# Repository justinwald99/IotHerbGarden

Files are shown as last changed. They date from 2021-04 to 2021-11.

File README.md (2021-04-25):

# iot_herb_garden

## Installation / Environment Settings
In order prepare your environment to run the IoT Herb Garden System, first install python and the following python packages using the command "pip install {package name}" on both the computer and Rasperry Pi used for your system. The versions listed in the table are those that we ran the project with, but many packages will work with later versions.

| Package | Version |
|---| ---|
| Brotli | 1.0.9 |
| click | 7.1.2 |
| colorama | 0.4.4 |
| dash | 1.19.0 |
| dash-bootstrap-components | 0.12.0 |
| dash-core-components | 1.15.0 |
| dash-html-components | 1.1.2 |
| dash-renderer | 1.9.0 |
| dash-table | 4.11.2 |
| Flask | 1.1.2 |
| Flask-Compress | 1.9.0 |
| future | 0.18.2 |
| greenlet | 1.0.0 |
| itsdangerous | 1.1.0 |
| Jinja2 | 2.11.3 |
| MarkupSafe | 1.1.1 |
| numpy | 1.20.2 |
| paho-mqtt | 1.5.1 |
| pandas | 1.2.3 |
| pip | 20.2.3 |
| plotly | 4.14.3 |
| python-dateutil | 2.8.1 |
| pytz | 2021.1 |
| retrying | 1.3.3 |
| setuptools | 49.2.1 |
| six | 1.15.0 |
| SQLAlchemy | 1.4.9 |
| Werkzeug | 1.0.1 |

You will also need a working MQTT broker, and a wireless network to run the local system on. We used `mosquitto`, accessible from https://mosquitto.org/ . Mosquitto configuration file needs to contain the settings:
```
listener 1883
allow_anonymous true
```

Next, assemble the hardware following the schematic in `docs/iot_herb_garden_schematic_bb.png` using the parts list in `docs/report.pdf` or other compatable parts.

## Running IoT_Herb_Garden / How to Run the Code

Three programs must be run to operate the IoT_Herb_Garden system: `garden_manager.py`, `garden_monitor.py`, and `garden_web_server.py`, as well as the MQTT broker.

When running the system, `garden_monitor.py` must be run on the Raspberry Pi. We recommended that `garden_manager.py` and `garden_web_server.py` be run on a separate computer to increase performance, but they can be run from the Pi if you chose (note that both manager and web server must be run on the same machine due to requiring direct database access).

To start the system, first start the MQTT server. If using mosquittor, run the following command from the mosquitto directory:
```
mosquitto -c "{address of the config file}"
```

Next start `garden_manager.py` using the command:
```
python garden_manager.py {ip of MQTT broker}
```

Next start `garden_web_server.py` using the command:
```
python garden_web_server.py {ip of MQTT broker}
```

Next start `garden_monitor.py` using the command:
```
python garden_monitor.py {ip of MQTT broker}
```

At this point all portions of the system should be online. The web server can be accessed through most browsers using `localhost:{port}` where port can be found in the command line output of `garden_web_server.py`. Each program can be stopped individually without impacting the rest of the system, other than the MQTT broker, which when closed would require a full system restart.

## Operations / How to Interpret the Results

To view the status of the system and manage sensor and plant settings, use the web server as described in the previous section. Through Overview and History, you can view the past sensor data and pump operations of the system. Controls can be used to manually operate the water pumps. Configurations can be used to change system settings on plant and sensor names, sensor sample rates, plant watering durations and soil humidity targets, and assign sensors and pumps to plants.

## Sample Input Files

Provided in the source code is a databse with data from our setup and testing. This data can be used through the web server to view how your data would look and test setting database values. Without any historical data, the system will generate a blank databse with default entries for plants and sensors. 

## Extra Information

This system was designed for a specific setup of four plants, but with minor alterations, many portions of the system could be extrapolated for larger or smaller setups. In order to understand the control flow and operations, we recommend reading the report found in `docs/`.

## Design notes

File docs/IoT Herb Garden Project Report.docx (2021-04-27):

CSC453: Internet of Things

April 25th, 2021

Parker Killian

Justin Wald

Michael Barger

Individual Contributions

Component | Weight | Parker Killian | Justin Wald | Michael Barger
Architecture Design | 0.1 | 33.3% | 33.3% | 33.3%
Frontend Design | 0.05 | 10% | 80% | 10%
Wiring Design | 0.05 | 20% | 40% | 40%
Hardware Assembly | 0.05 | 33.3% | 33.3% | 33.3%
Web Server | 0.15 | 50% | 30% | 20%
Garden Monitor | 0.15 | 50% | 25% | 25%
Garden Manager | 0.15 | 25% | 65% | 10%
Debugging | 0.1 | 10% | 10% | 80%
Presentation | 0.05 | 80% | 10% | 10%
Report | 0.1 | 20% | 40% | 40%
Documentation | 0.05 | 10% | 10% | 80%
Total Contributions | | 32.745% | 34.995% | 32.245%

# Introduction

When attempting to grow an herb garden, it can be difficult to remember to water your plants or to keep the soil humidity levels at an appropriate level. The objective of this project is to simplify this process by Internet of Things automation

The goal of this project was to create an automated garden management system that uses an array of sensors and water pumps to monitor the environment and automatically water the plants in an herb garden. This system would provide detailed information to the user of the status of their plants as well as allowing for a large amount of user customization to tailor the system to the user’s plants’ needs

# Design

## Architecture

IoT Herb Garden is comprised of 3 primary python scripts:

Garden Manager | Garden Monitor | Garden Web Server
- Create database schema objects. - Log sensor and event data to the database when received from the MQTT broker. - Provide auto-watering functionality. - Inform other components of configuration info read from the database. | - Configure defaults for sensors. - Collect and publish sensor data. - Activate water pumps when instructed to do so. | - Provide a web UI to interact with the Herb Garden - Display current metrics for sensors - Display a historic view of sensor values - Allow configuration of plant and sensor objects - Manually control pumps

Table 1: Script Overview

The separation of these three scripts gives the user flexibility in the hardware running each. The monitor script was kept lightweight to facilitate operation on an edge device such as a Raspberry Pi. Manager communicates with the monitor entirely through MQTT which means that it can run on an entirely different host, as long as they share the same broker. Web server does need access to the database to operate which ties it to running on the same host as manager since we used SQLite as our backend but with a little modification, web server could also run on its own host. Containerizing the entire system would be quite trivial thanks to this separation.

One other advantage of this architecture is that the more critical scripts, manager and monitor, could operate in “headless” mode without the web server running, only logging data to the DB. This also means that if the web server crashes for whatever reason, logging will continue.

Figure 1: MQTT architecture between the scripts

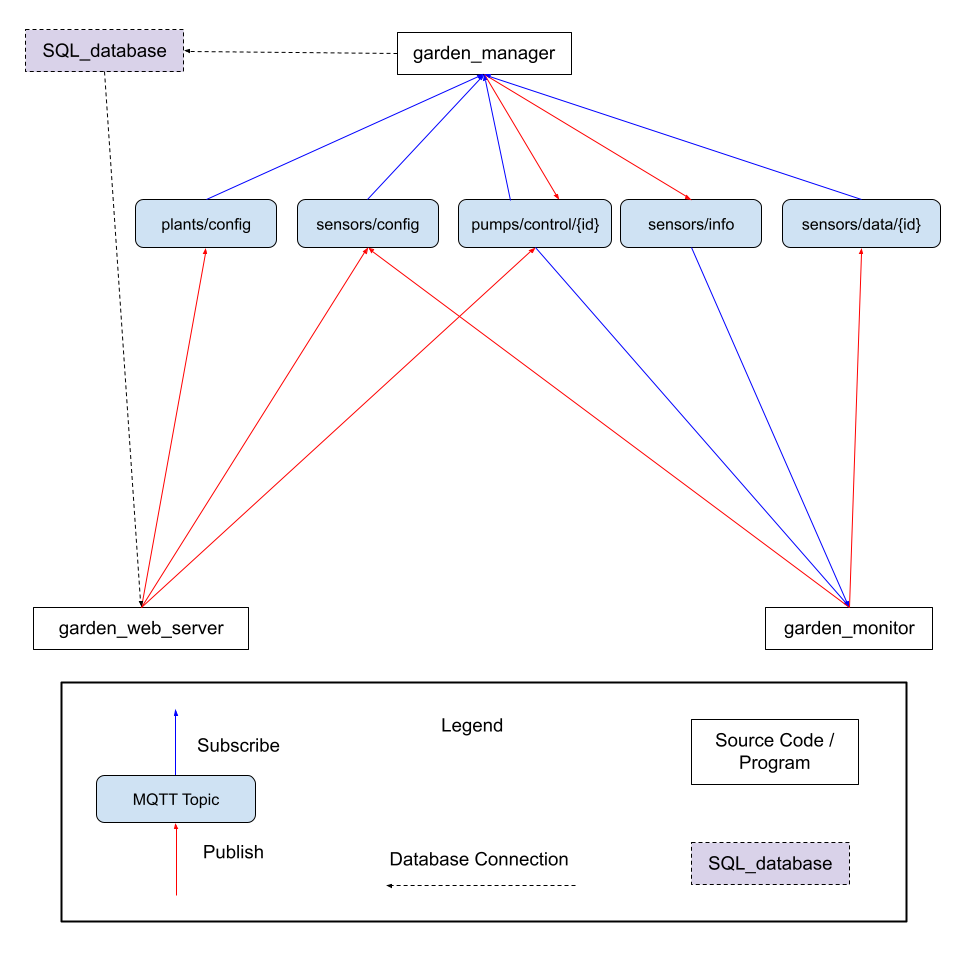
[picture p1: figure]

## MQTT

Communication between the different parts of our program is done primarily through MQTT, leveraging an outside broker. Below is a diagram showing the interaction between each component through MQTT messages. Each message contains a JSON payload (described in Appendix 1) to communicate the body of the messages.

A typical flow for the program is shown in figure 2 and follows these steps:

1. Monitor starts and begins logging sensor data with a default configuration file loaded from a static JSON File.
2. Manager reads any configuration data from the database and publishes this data to the sensors/info topic.
3. Monitor, which is subscribed to this topic, receives the information and compares it against the default values it has.
  a. If there are any differences, the information from the manager is preferred.
  b. If there are no sensors in the message published by the manager, such as in the case of a reset database, monitor publishes its default values to sensors/config, one at a time. Manager reads these messages and adds them to the sensors/info message.
4. Monitor begins sending sample messages to sensors/data.
5. Manager, subscribed to sensors/data, writes these messages to the database.
6. Manager also monitors sensor values to determine if watering is needed.

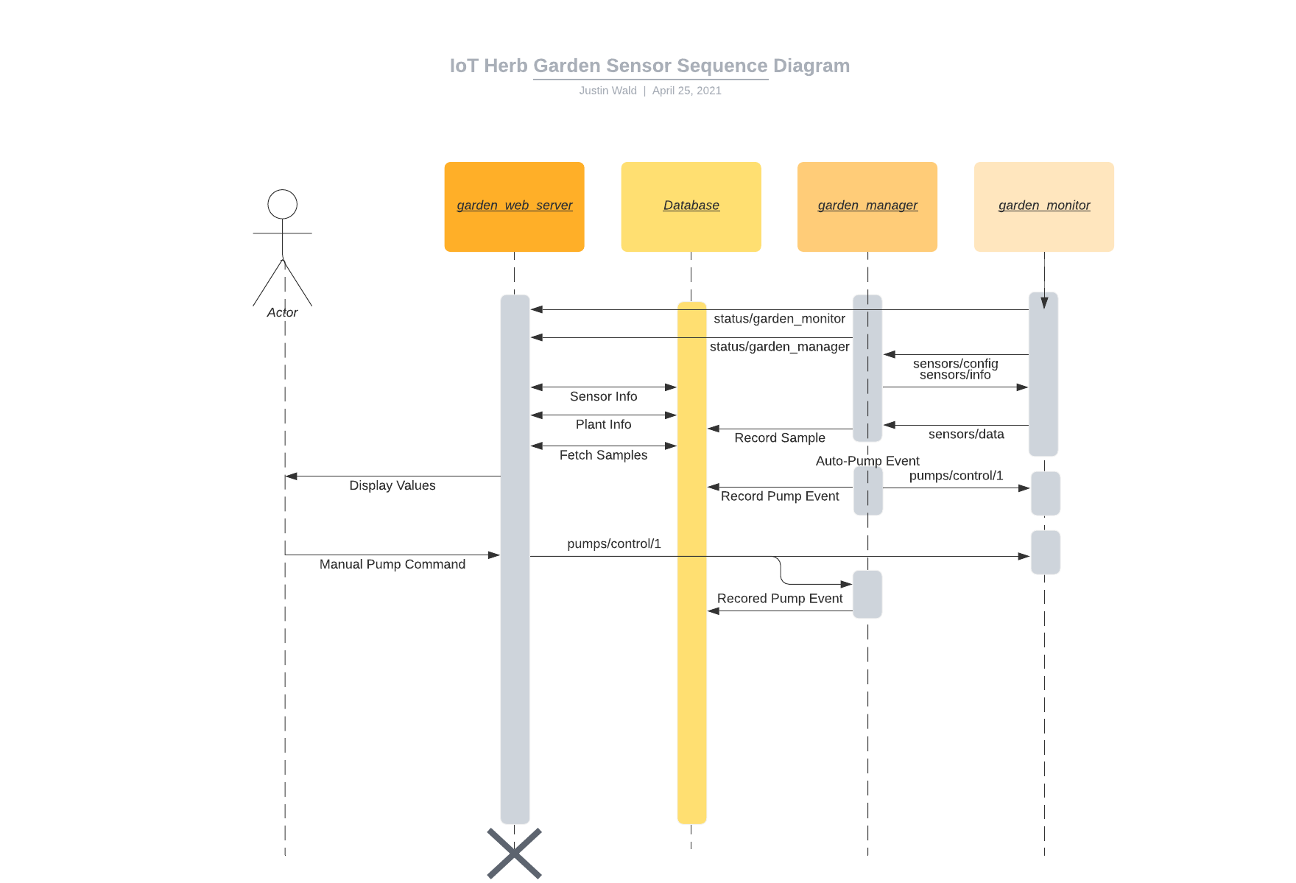
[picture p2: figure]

Figure 2: Sequence diagram of a basic flow through the system.

## Database

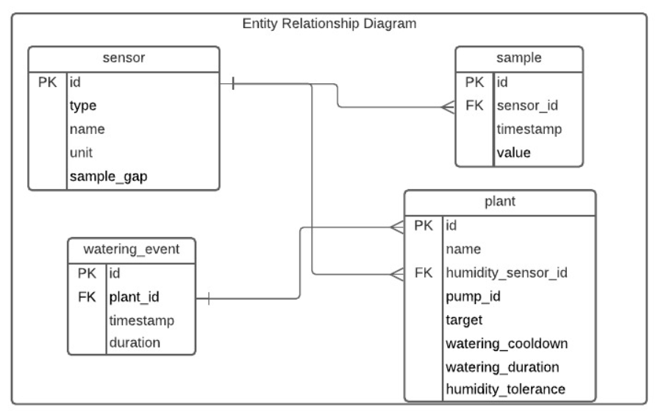
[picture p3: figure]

Figure 3: ERD diagram for the database.

The database is based on a SQLite backend which we accessed via SQLAlchemy for consistency and reliability. The database was used primarily to record data so that historical viewing was possible but it also enabled persistent settings to be specified by the user about the elements of the system.

## Web Server

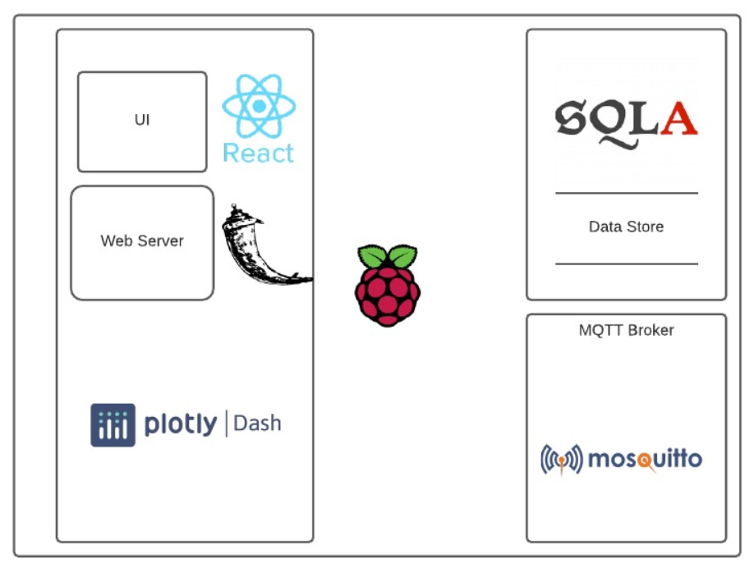
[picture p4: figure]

Figure 4: Technology overview.

The web server uses the Dash library which makes use of the highly popular Flask library for its web server operations while providing a robust React-based UI toolkit that includes the Plotly graphing library.

# Implementation

Our project runs on Python, using many public libraries for specific operations including SQLAlchemy, Dash, Dash Bootstrap Components, Pandas, Paho MQTT, and GPIOZero.

The hardware for our project included:

- Raspberry Pi 3b+
- A breadboard
- A prototyping board
- 4 capacitive soil humidity sensors
- 4 5V impeller water pumps
- 4 PCB-mounted 5V relays
- A DHT22 (thermistor / hygrometer combo)
- A photoresistor
- An 8 channel ADC
- 22 Awg wires

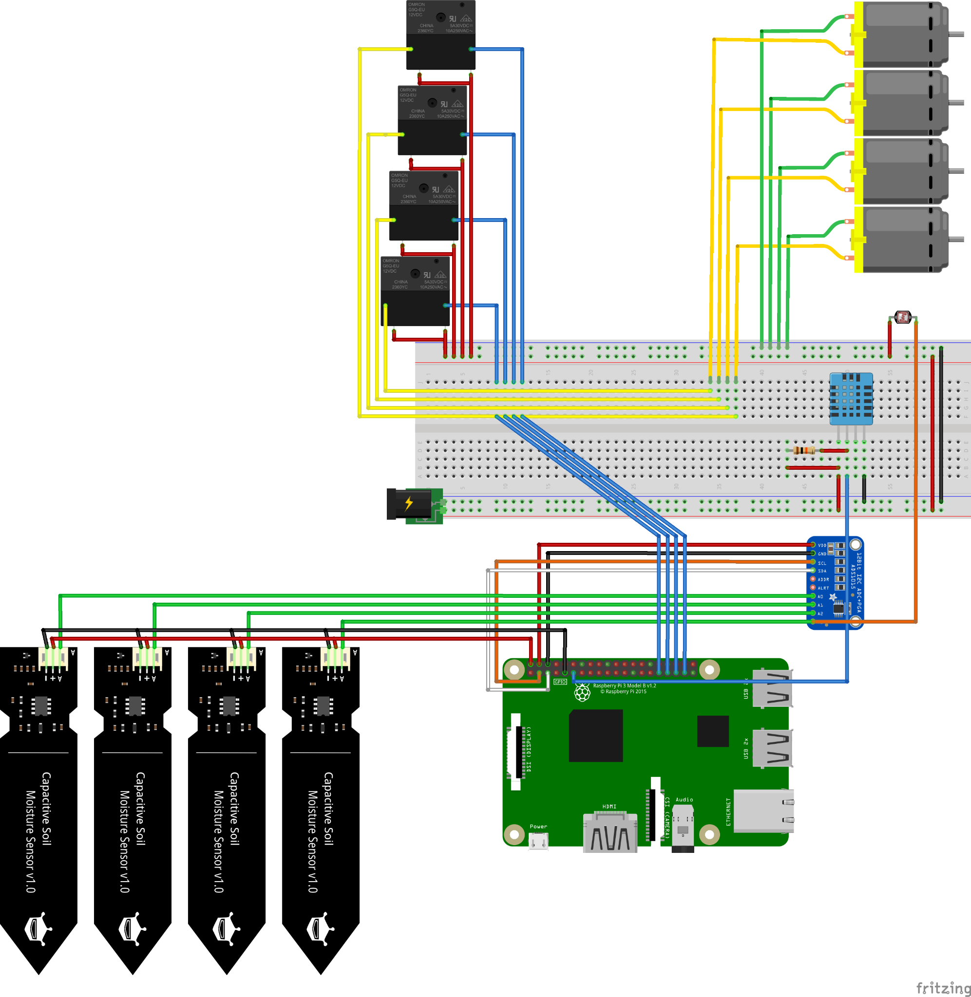
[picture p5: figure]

Figure 4: Wiring Schematic

To run the IoT_Herb_Garden system, it is necessary to run 3 programs, garden_manager.py, garden_monitor.py, and garden_web_server.py. While it is necessary for the garden monitor to run on the Raspberry Pi, it is recommended that manager and web server both run on a more powerful computer to increase performance.

## garden_manager.py

Garden manager acts as the brains of the system. It handles recording MQTT messages to the database and automatically triggering pump operations based on sensor data.

## garden_monitor.py

Garden monitor runs all of the sensors, pumps, and hardware for the project. On startup, and when a message is received from “sensors/info”, it updates its local values for sensor sample rates. Its sensors then sample based on their set sample rate, and the values are published to the MQTT topic “sensors/data/{id}”. When it receives a message from “pumps/control/{id}”, a locking thread is created that runs the pump for the provided duration. If multiple pump operations are received in quick succession, the locking threads ensure that only one pump runs at a time, limiting the current draw on the Raspberry Pi.

## garden_web_server.py

Garden web server works in tandem with app.py and the files in apps/ to create and run the website for the IoT Herb Garden system. The Overview and History pages provide graphical views of the sensor and pump history, while Controls and Configuration allow for user interaction with the system. Through the Controls page, users can provide pump durations to send manual pump operations through MQTT over the “pumps/control/{id}” topic. These messages are stored in the database and trigger the indicated pumps to operate for the given duration. The Configuration page allows for the user to change the settings of each parameter of the Plants and Sensors in the system. The parameters affect the displays on the Overview and History pages as well as the operating settings of the Raspberry Pi and garden manager. Through the web server, all aspects of the system can be controlled and monitored remotely.

## utils/

Each source file in the utils/ directory is used by at least one of the three main programs. adc_library.py is used to interface with our adc. common.py contains common functions that can be used system wide. db_interactions.py is used primarily by garden_manager to create database entries. sensors.py is used primarily by garden_monitor to interface with the other sensors in the system. ui_elements is used to create graphics on garden web server pages.

# Results and Discussion

While we did not intend too much in the way of analysis, we have noticed some interesting trends in our sensor setup. The above graphic shows the history of sensor values over several hours. With these readings, you can see a very clear relationship between ambient temperature and ambient humidity. As temperature increases, the air is able to hold more humidity which decreases the relative humidity. Notably, these changes don’t have a significant short-term effect on the humidity of any of the soil humidity sensors. Visible in the history graph at approximately 16:00 is a pump operation. The large spike in soil humidity comes from the water soaking into the soil at the level of the humidity sensor. The gradual settling into a lower level comes from the water soaking in and spreading out in the soil.

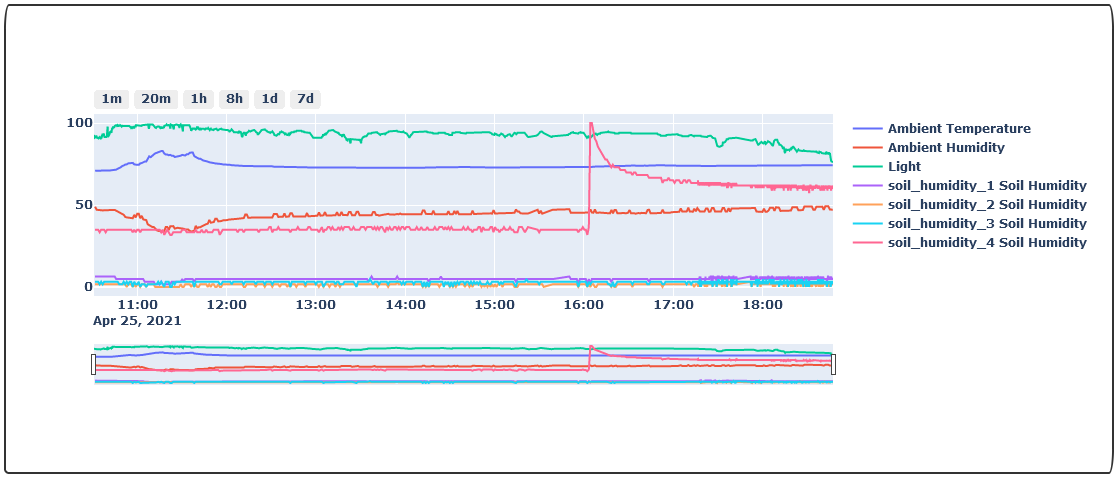
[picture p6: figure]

Figure 5: Data from History Page Graph

# Appendix 1 - MQTT

## status/garden_manager

Retained: True

Format:
online

Goodwill_message:
offline

## status/garden_monitor

Retain: True

Format:
online

Goodwill_message:
offline

## sensors/info

Retained: True

Purpose: Tell the other programs about what sensors are connected to garden_monitor.py

Format:

[

{

id: <int>,

type: <string>,

name: <string>,

unit: <string>,

sample_gap: <int>

},

{

id: <int>,

type: <string>,

name: <string>,

unit: <string>,

sample_gap: <int>

},

]

## sensors/data/{id}

Retained: False

Purpose: Publish as single data sample

Format:

{

timestamp: <ISO>,

value: <value>

}

## pumps/control/{pump_id}

Retained: False

Purpose: Instruct garden_monitor to run the pumps for a set duration.

Format:

{

duration: <seconds>

}

## plants/config

Retained: True

Purpose: Tell garden_manager about the configured plants.

Format:

{

id: <id>

name: <name>,

humidity_sensor_id: <sensor_id>,

pump_id: <pump_id>,

target: <[0, 100]>,

watering_cooldown: <[5, 300]>,

watering_duration: <(0, 5]>,

humidity_tolerance: <[0, 50]>

}

## sensors/config

Retained: True

Purpose: Tell garden_manager about the configured plants.

Format:

{

id: <int>,

type: <string>,

name: <string>,

unit: <string>,

sample_gap: <int>

}

# Appendix 2 - Web Pages

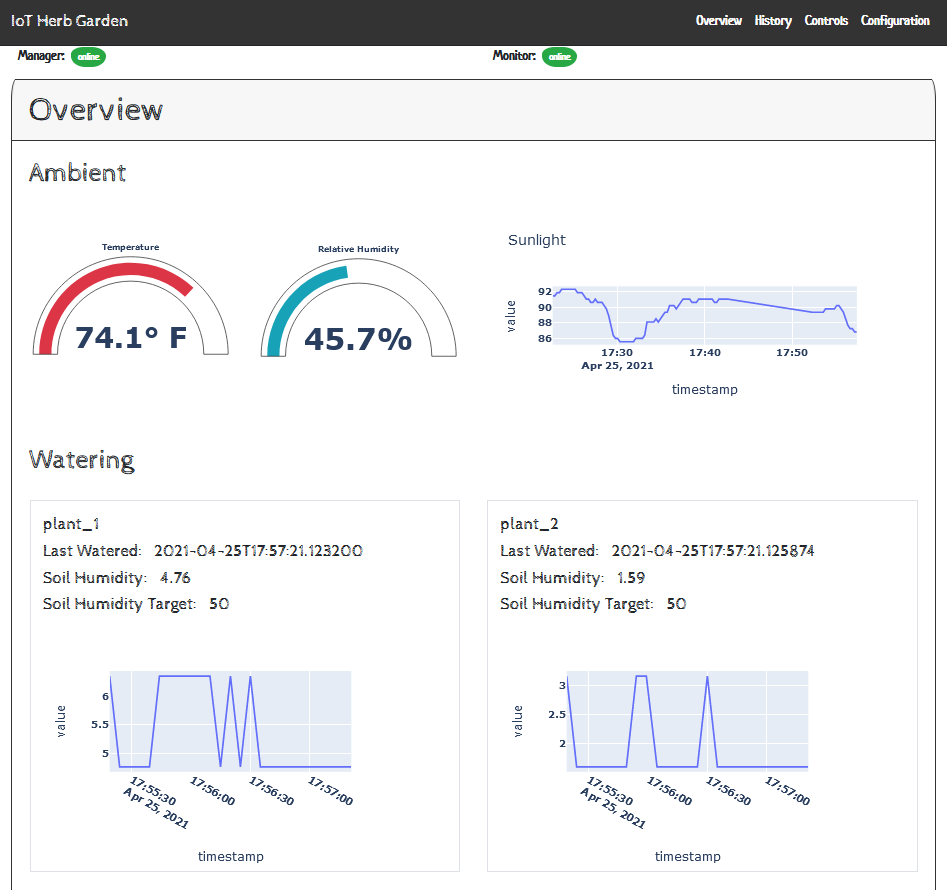
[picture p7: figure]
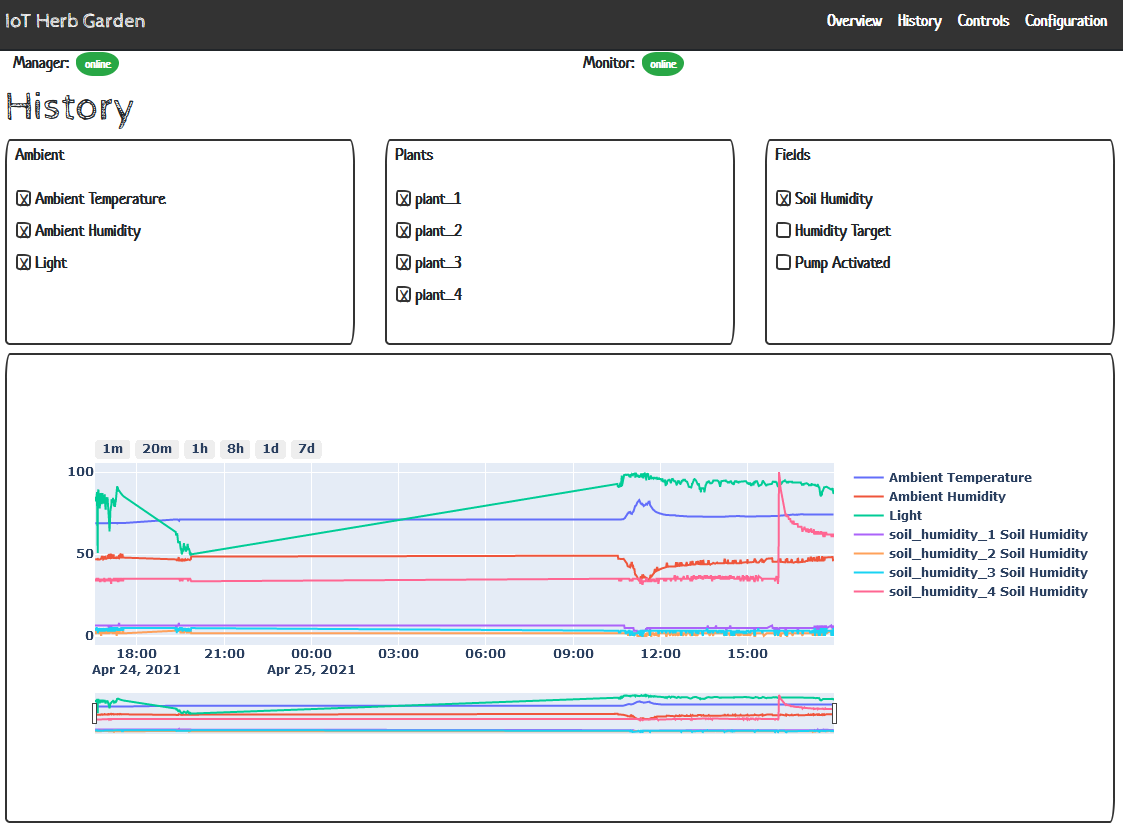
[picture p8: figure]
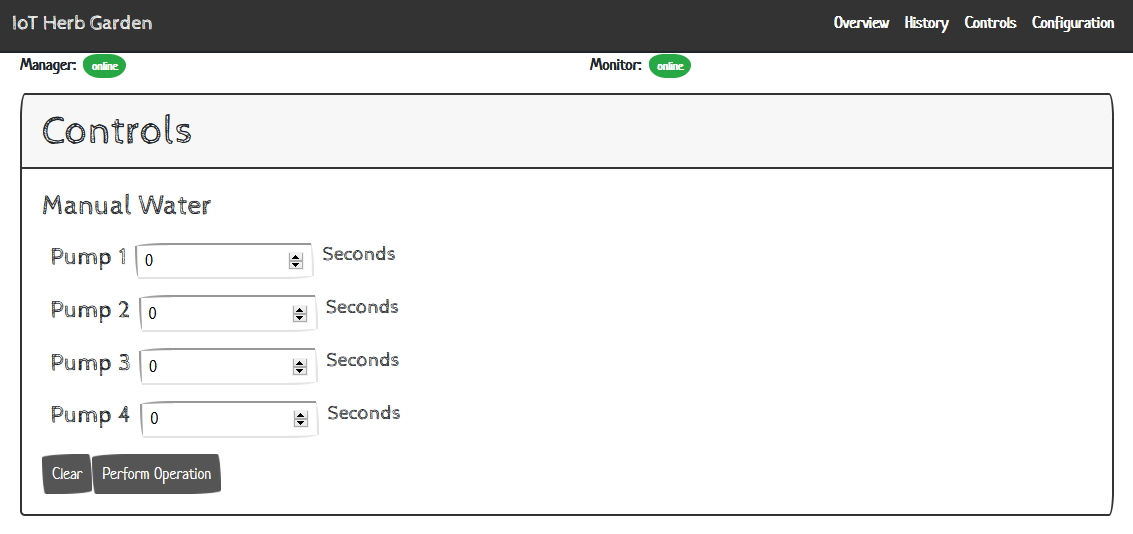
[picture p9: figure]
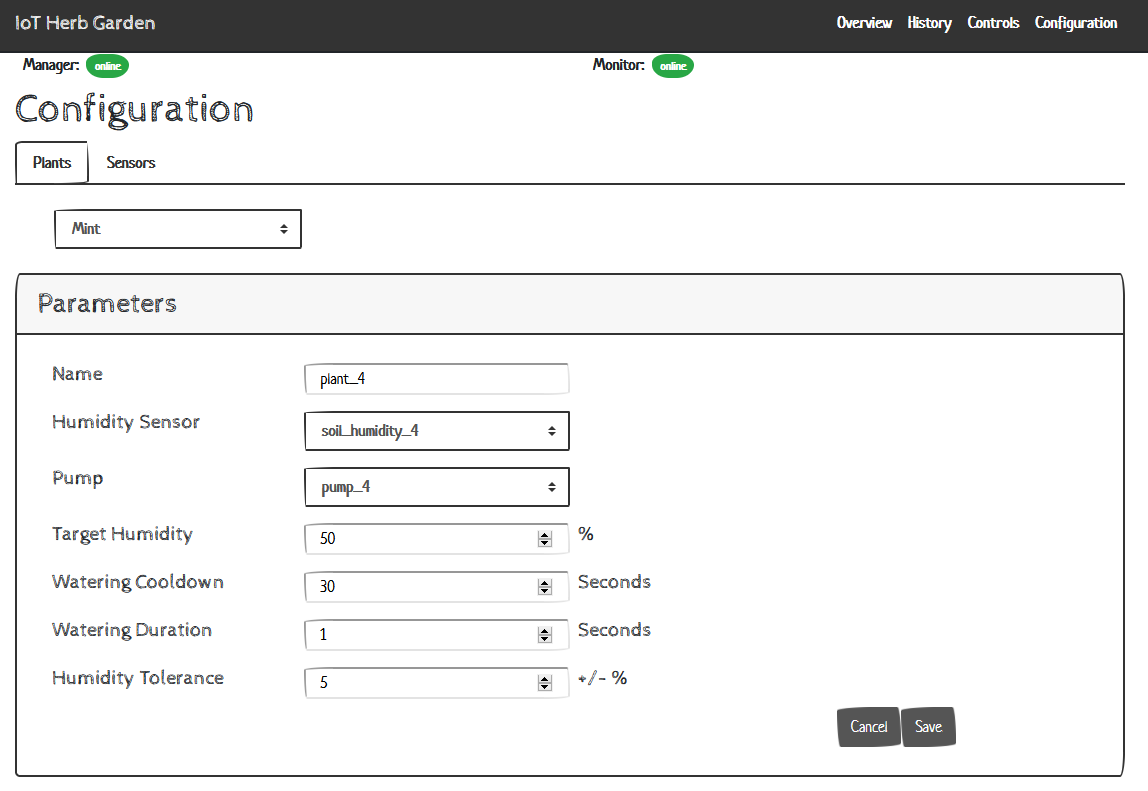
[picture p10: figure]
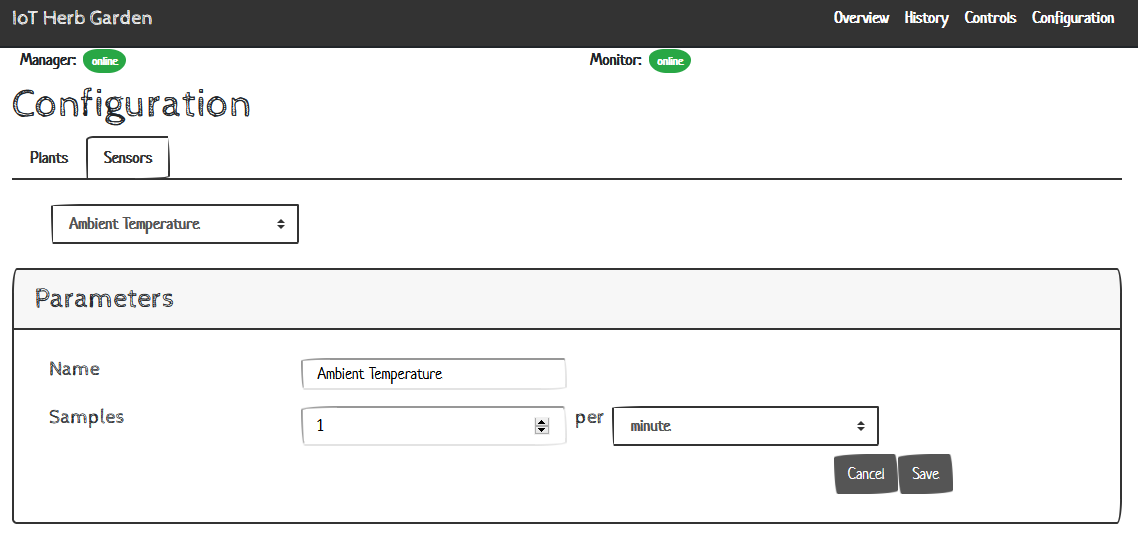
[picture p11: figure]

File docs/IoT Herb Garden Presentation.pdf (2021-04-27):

# IoT Herb Garden

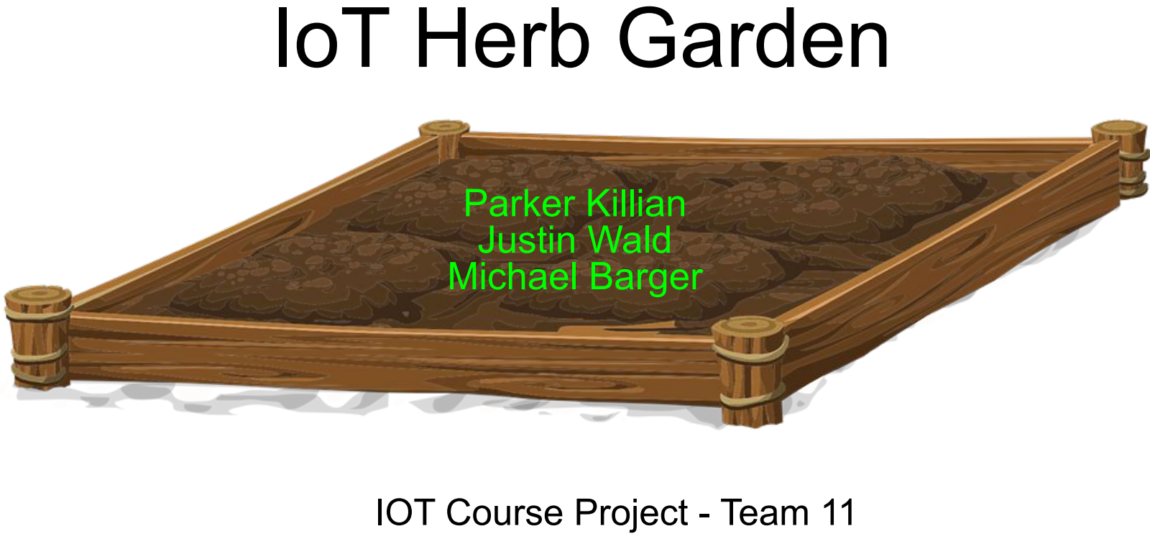
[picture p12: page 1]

# IOT Course Project - Team 11

# Parker Killian Justin Wald Michael Barger

# Project Goals

## - Automate watering of plants - Log the environment attributes and soil watering - Use these logs to display graphs in a web server - Allow the web server to edit configuration of plants, send manual pumps

# Database Structure

- Sensor
- Stores information of each sensor in the system
- Plant
- Stores information about each plant in the system
- Connects plants to their sensor and pump
- Controls when to water the plant
- Sample
- Stores data from individual samples from the sensors
- Watering_event
- Stores a record of pump operations

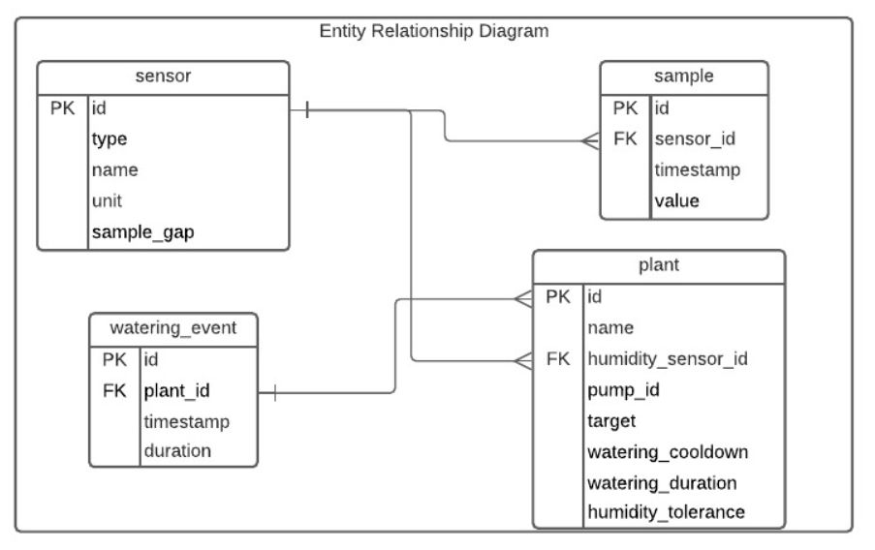
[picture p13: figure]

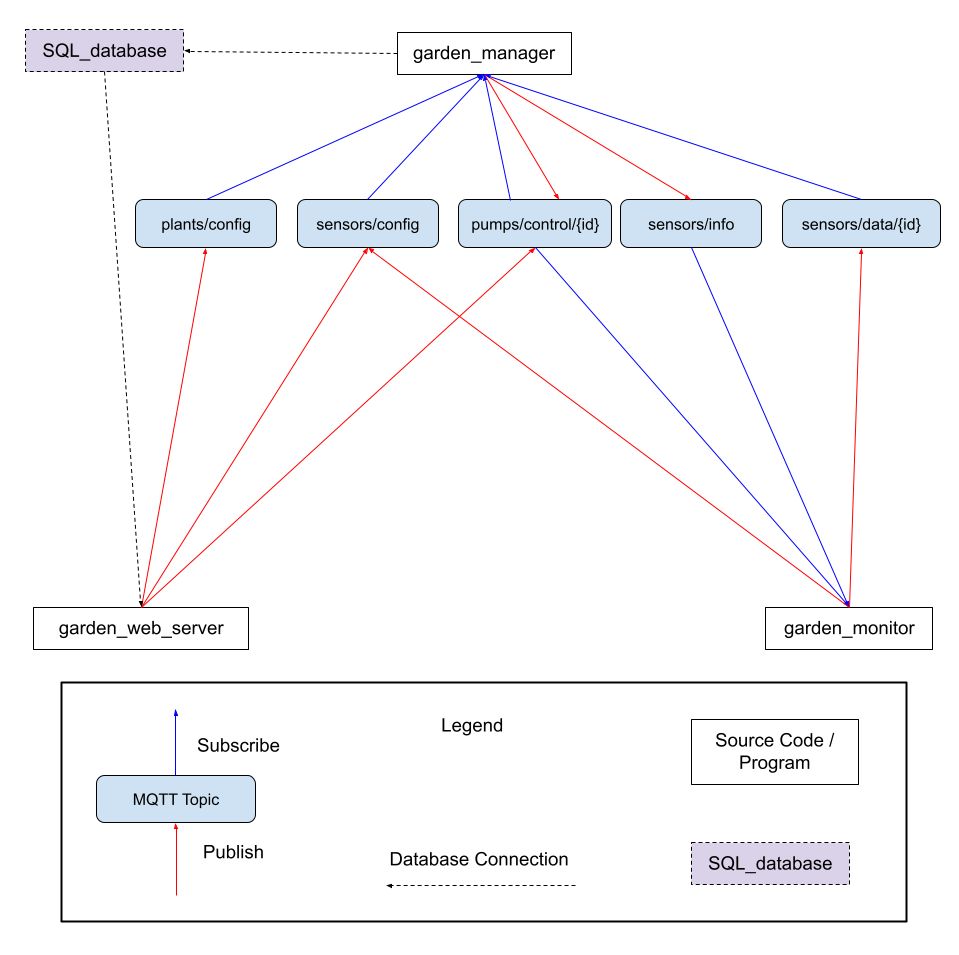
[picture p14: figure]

# MQTT Topics

Configuration information, sensors data, and pump controls are sent over MQTT to communicate between the system components. Data not sent over MQTT is stored and accessed through an SQL database.

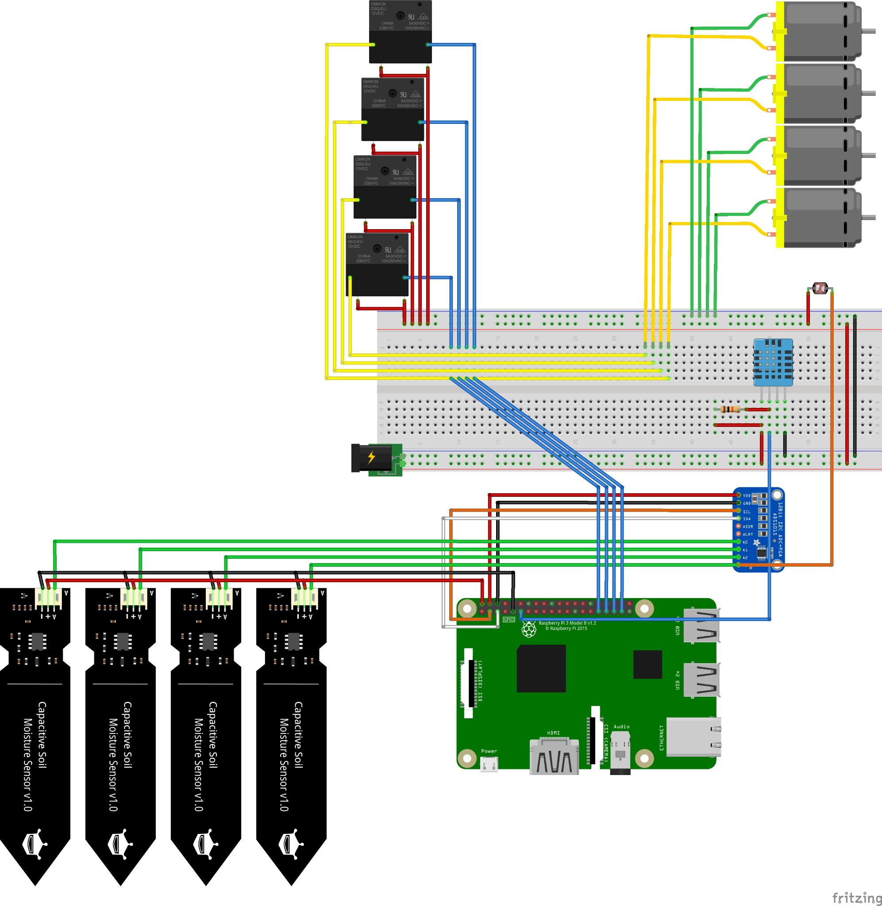
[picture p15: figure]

# Hardware

- Raspberry Pi 3b+
- A breadboard
- A prototyping board
- 4 capacitive soil humidity sensors
- 4 5V impeller water pumps
- 4 PCB-mounted 5V relays
- A DHT22 (thermistor /
hygrometer combo)
- A photoresistor
- An 8 channel ADC
- 22 Awg wires

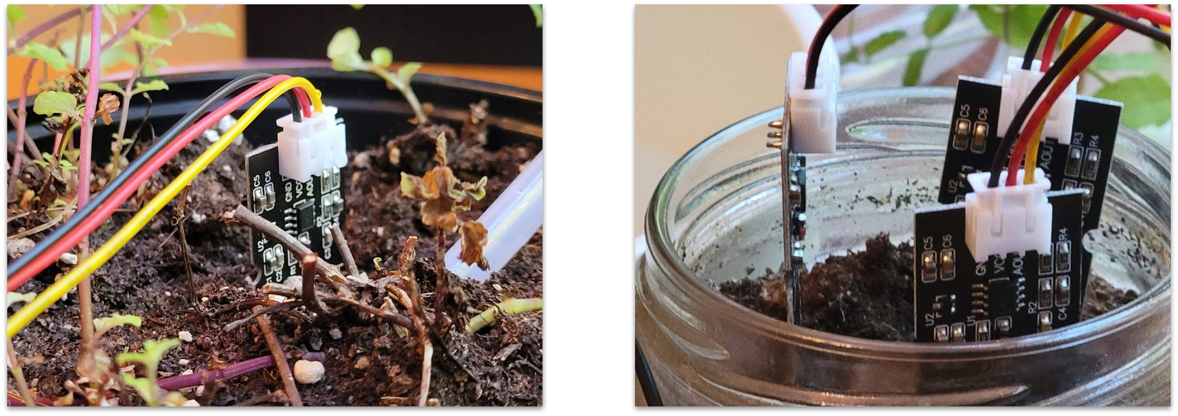
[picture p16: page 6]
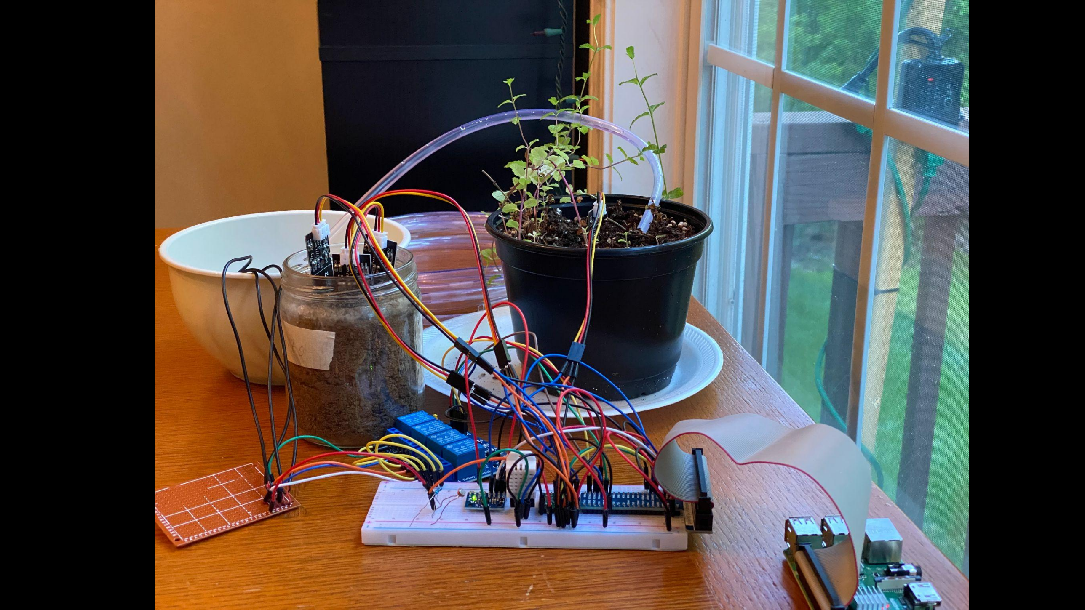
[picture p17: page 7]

# Implementation

- Our project is built in Python using the libraries: Dash (web server), SQLAlchemy (database), Paho-MQTT, and GPIOZero
- Three programs to run:

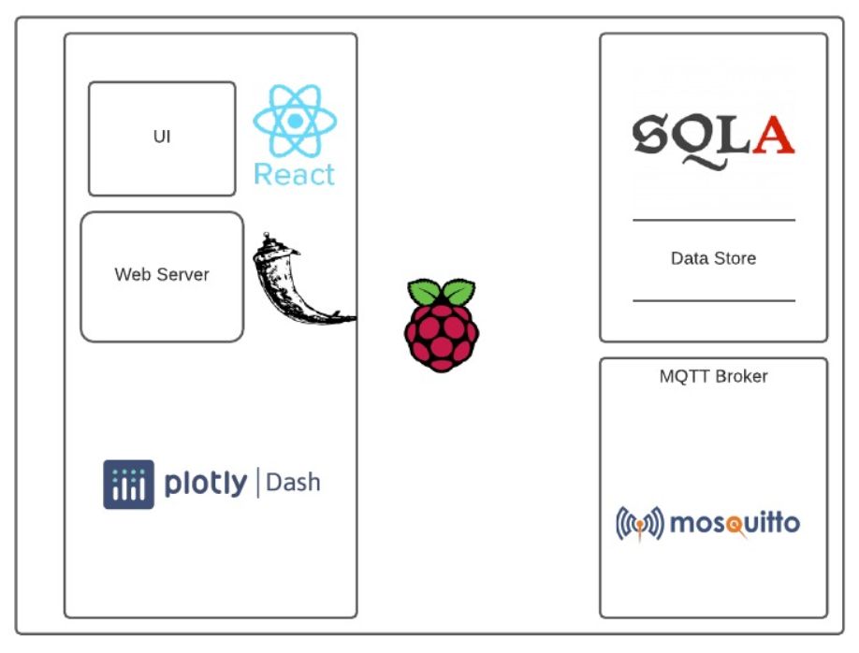
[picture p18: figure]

Garden Manager | Garden Monitor | Garden Web Server
❖ | Create database schema
objects.
❖ Log sensor and event data to the database when received from the MQTT broker.
❖ Provide auto-watering
functionality.
❖ Inform other components of configuration info read from the database.
❖ | Configure defaults for sensors.
❖ | Collect and publish sensor data.
❖ | Activate water pumps when
instructed to do so.

❖ Provide a web UI to interact with the Herb Garden
❖ Display current metrics for sensors
❖ Display a historic view of sensor values
❖ Allow configuration of plant and sensor objects
❖ Manually control pumps

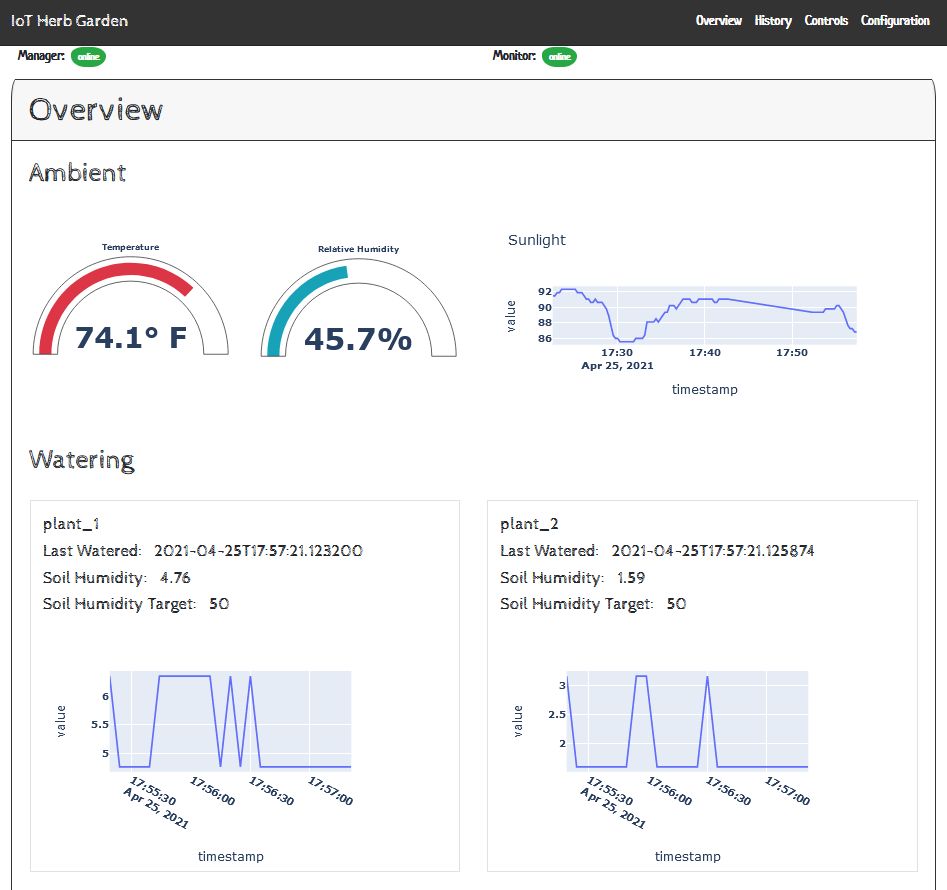
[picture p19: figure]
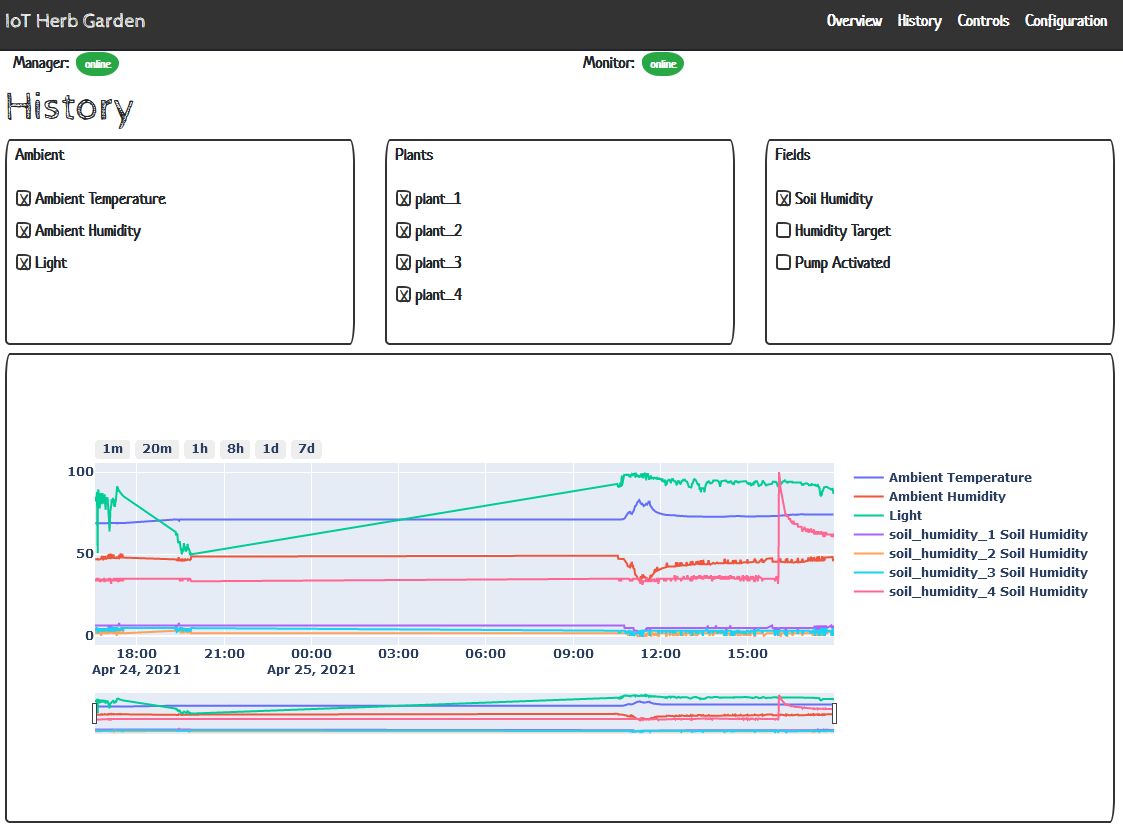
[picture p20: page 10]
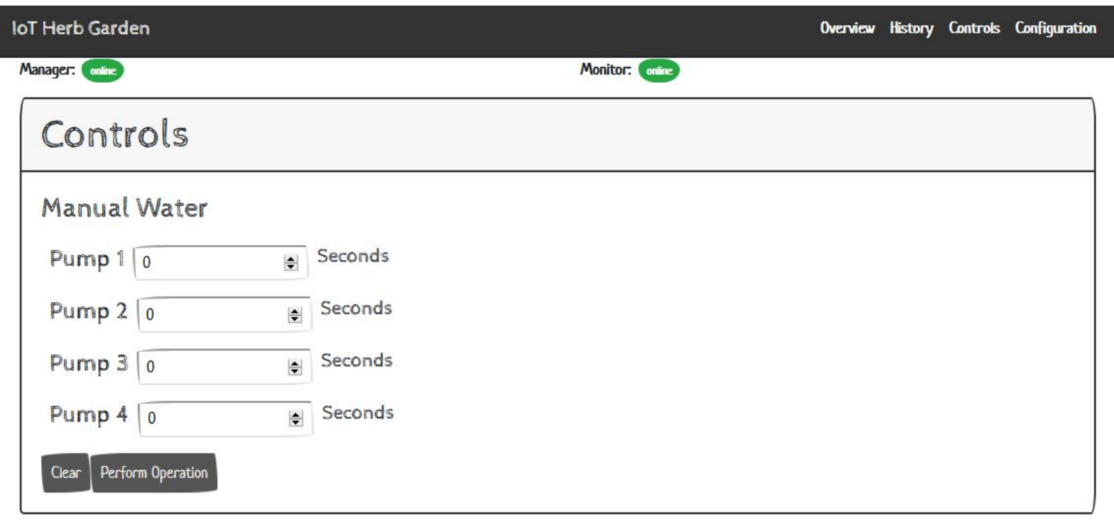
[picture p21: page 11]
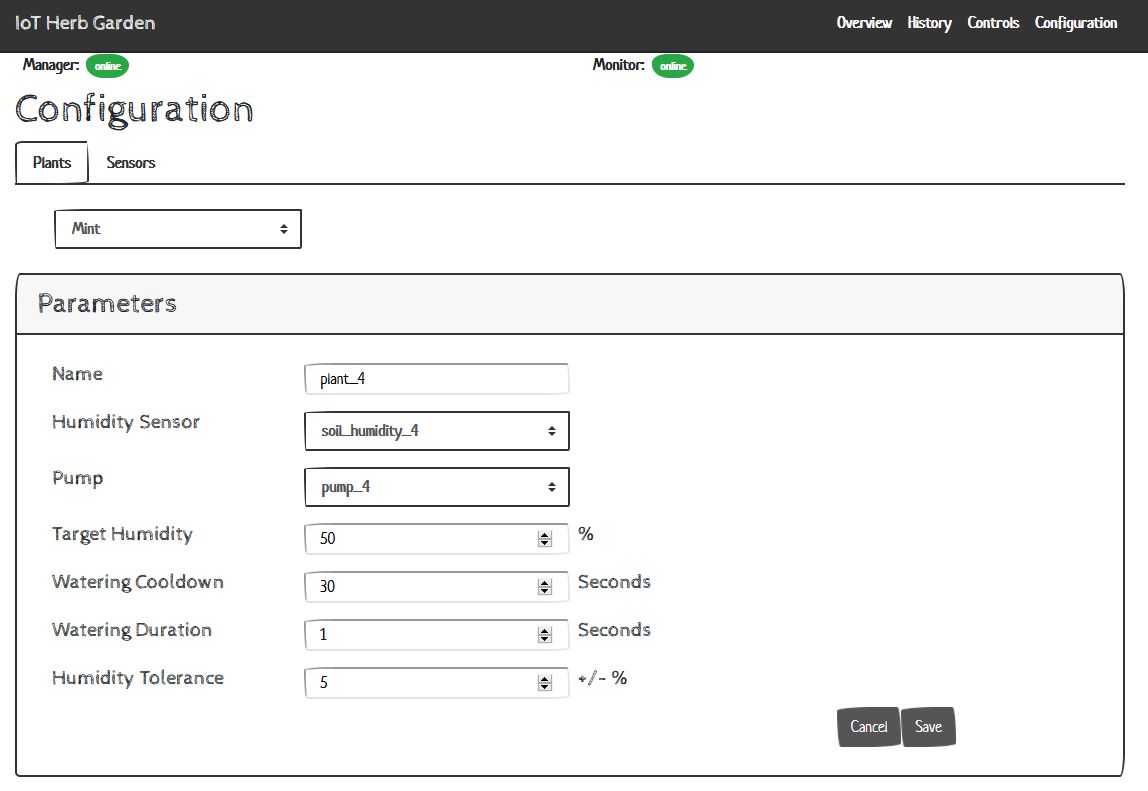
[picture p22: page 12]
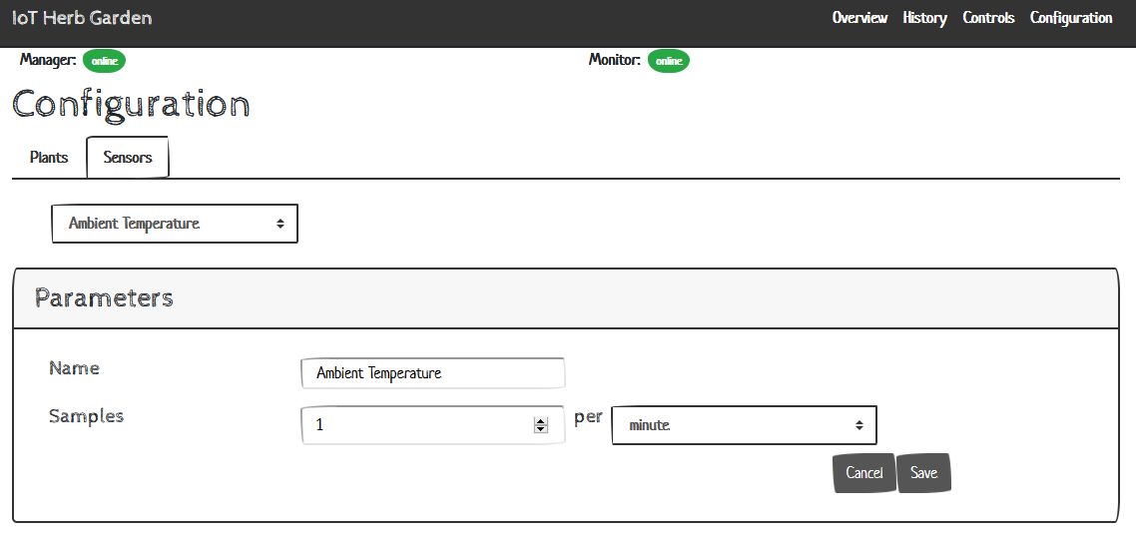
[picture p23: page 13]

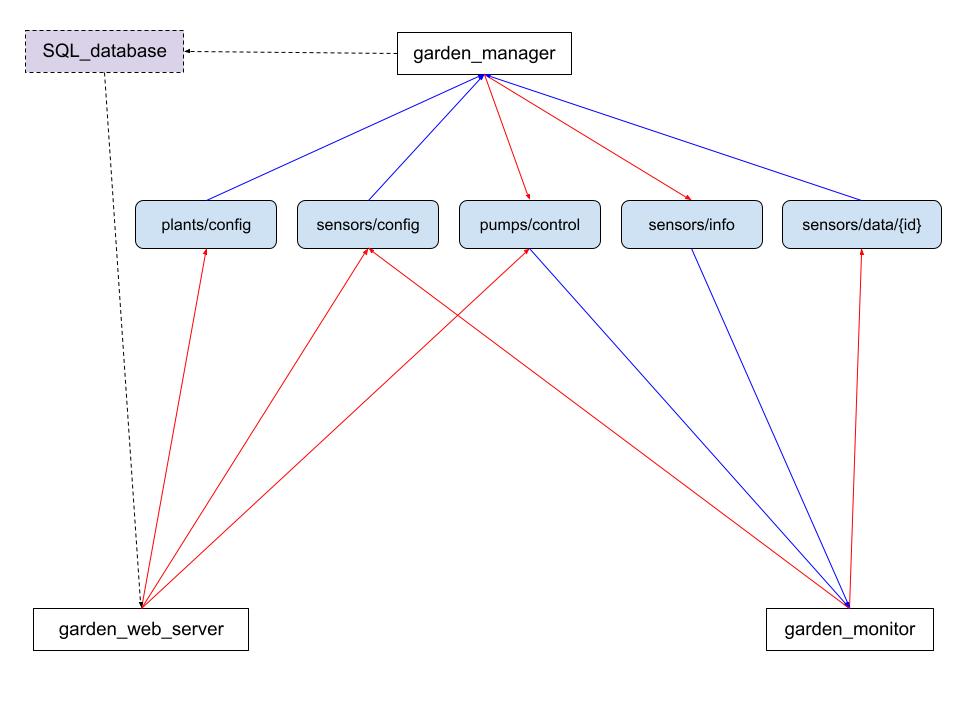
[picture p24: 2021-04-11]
docs/images/iot_herb_garden MQTT map.jpg

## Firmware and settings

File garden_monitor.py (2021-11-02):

"""Monitor that runs on the pi to collect sensor data and run pumps."""
import json
import os
import threading
import time
from datetime import datetime as dt

import board
import paho.mqtt.client as mqtt
import yaml
from gpiozero.output_devices import OutputDevice

from utils.adc_library import ADS7830
from utils.common import connection_message, parse_json_payload
from utils.logging import (config_logger, mqtt_logger, pump_logger,
                           sample_logger)
from utils.sensors import (ambient_humidity, ambient_temperature, dht_22,
                           light, soil_humidity)

# Create the MQTT client
client = mqtt.Client("garden_monitor")

# IP for the MQTT broker
broker_host = ""

# Config to hold sensor config data
sensor_config = {}

# Sensor dictionary with sensor values that can be sampled
sensors = {}

# Make an object to interact with the analog-to-digital converter
adc = ADS7830()

# Object used to control access to the dht-22 sensor
dht_22 = dht_22(board.D17)

# Register pumps on GPIO pins
pump1 = OutputDevice("GPIO26", active_high=False)
pump2 = OutputDevice("GPIO19", active_high=False)
pump3 = OutputDevice("GPIO13", active_high=False)
pump4 = OutputDevice("GPIO6", active_high=False)

# Threading lock to prevent concurrent pump activation
pump_lock = threading.Lock()

# Map pump ids to their pump objects
pump_mapping = {
    "1": pump1,
    "2": pump2,
    "3": pump3,
    "4": pump4
}


def read_config():
    """Read the config JSON that contains known info about the sensors connected.

    This data needs to be reconciled with known data from sensors/info before building.
    """
    with open("sensor_config.yaml", "r") as config_file:
        config = yaml.safe_load(config_file.read())
    config_logger.info(f"Loaded config: {json.dumps(config, indent=4)}")
    return config


def build_sensors():
    """Build sensor objects from the configuration stored in sensors."""
    config_logger.info(
        f"Reconciled config: {json.dumps(sensor_config, indent=4)}")
    for id, sensor in sensor_config.items():
        if (sensor["type"] == "soil_humidity"):
            new_sensor = soil_humidity(
                id, adc, sensor["adc_index"], unit=sensor["unit"],
                sample_gap=sensor["sample_gap"], dry_value=sensor["dry_value"],
                wet_value=sensor["wet_value"]
            )
            sensors.update({new_sensor.id: new_sensor})

        if (sensor["type"] == "ambient_humidity"):
            new_sensor = ambient_humidity(
                id, dht_22, unit=sensor["unit"], sample_gap=sensor["sample_gap"]
            )
            sensors.update({new_sensor.id: new_sensor})

        if (sensor["type"] == "ambient_temperature"):
            new_sensor = ambient_temperature(
                id, dht_22, unit=sensor["unit"], sample_gap=sensor["sample_gap"]
            )
            sensors.update({new_sensor.id: new_sensor})

        if (sensor["type"] == "light"):
            new_sensor = light(
                id, adc, sensor["adc_index"], unit=sensor["unit"],
                sample_gap=sensor["sample_gap"], dark_value=sensor["dark_value"],
                light_value=sensor["light_value"]
            )
            sensors.update({new_sensor.id: new_sensor})
        config_logger.info(
            f"Created {sensor['type']} sensor with id: {sensor['id']}")


def activate_pump(pump_id, duration, lock):
    """Activate pump for a specified amount of time, ensuring that only one pump runs at a time.

    Parameters
    ----------
    pump : int
        ID of the pump to activate.

    duration : int
        Number of seconds to run the pump.

    lock : threading.Lock()
        Lock primitive to prevent pumps running concurrently which may draw too much current.
    """
    pump = pump_mapping[pump_id]
    with lock:
        pump_logger.info(f"Pump {pump_id} activated")
        pump.on()
        time.sleep(duration)
        pump.off()
        pump_logger.info(f"Pump {pump_id} deactivated")


def sample_routine():
    """Run the main routines of the program.

    Collects data from the sensors if their sample_gap has elapsed since the last collection
    event. Then checks for MQTT messages.
    """
    for id, sensor in sensors.items():
        if (dt.now() - sensor.last_sample).total_seconds() > (sensor.sample_gap):
            value = sensor.sample()
            timestamp = dt.now()
            payload = {
                "value": value,
                "timestamp": timestamp.isoformat()
            }
            client.publish(f'sensors/data/{id}',
                           payload=json.dumps(payload), qos=2)
            sample_logger.info(
                f"Published {value}{sensor.unit} for sensor_id {id}")


def handle_pumps_control(client, userdata, msg):
    """Activate a specified pump when a message is received on pumps/control/{id}."""
    data = parse_json_payload(msg)
    mqtt_logger.info(
        f"Pump instruction received: {json.dumps(data, indent=4)}")

    pump_id = msg.topic.split("/")[-1]

    new_thread = threading.Thread(target=activate_pump, args=(
        pump_id, data["duration"], pump_lock))
    new_thread.start()


def handle_sensor_info(client, userdata, msg):
    """Reconcile known sensor info from garden_manager with local config."""
    global sensors
    known_sensors = parse_json_payload(msg)
    mqtt_logger.info(
        f"Received config from sensors/info: {json.dumps(known_sensors, indent=2)}")

    # For sensors that are passed, we change our local config
    for known_sensor in known_sensors:
        # Check for sensor_id matches in the known config vs local
        if str(known_sensor["id"]) in sensor_config.keys():
            sensor_config[str(known_sensor["id"])].update(
                {
                    "type": known_sensor["type"],
                    "name": known_sensor["name"],
                    "unit": known_sensor["unit"],
                    "sample_gap": known_sensor["sample_gap"]
                }
            )
    # For sensors that sensors/info didn't know about, we send a default config to sensors/config
    known_ids = [str(sensor["id"]) for sensor in known_sensors]
    for id, sensor in sensor_config.items():
        if id not in known_ids:
            payload = {
                "id": id,
                "type": sensor["type"],
                "name": sensor["name"],
                "unit": sensor["unit"],
                "sample_gap": sensor["sample_gap"]
            }
            mqtt_logger.info(
                f"Publishing new sensor config for sensor_id {id}")
            client.publish("sensors/config",
                           payload=json.dumps(payload), qos=2, retain=False)

    # Once config has been reconciled, build sensors.
    build_sensors()


def publish_status(client, userdata=None, flags=None, rc=None):
    """Publish the status of garden_monitor."""
    mqtt_logger.info(connection_message(broker_host, rc))
    client.publish("status/garden_monitor",
                   payload="online", qos=2, retain=True)
    mqtt_logger.info("Status published")


"""
On startup, sensor info is empty
garden monitor will call sensor config for each of the sensors not in sensor info
garden monitor gets current state from sensors info. If garden monitor has the sensors,
it will change the values it has if they are different. However, if garden monitor has
sensors unknown to sensors info, it will post a sensors/config for each one that is not
included.
"""
if __name__ == '__main__':
    # Set garden_monitor's last will message for when it is offline.
    client.will_set("status/garden_monitor",
                    payload="offline", qos=2, retain=True)

    # Set callback methods
    client.on_connect = publish_status
    client.message_callback_add("pumps/control/#", handle_pumps_control)
    client.message_callback_add("sensors/info", handle_sensor_info)

    # Connect to the MQTT broker
    client.connect(os.environ.get("MQTT_BROKER_HOST"), 1883)

    # Subscribe to applicable topics
    client.subscribe([
        ("sensors/info", 2),
        ("pumps/control/+", 2)
    ])

    # Send online message
    publish_status(client)

    # Load basic values in.
    sensor_config = read_config()

    build_sensors()

    # Start the main routine
    while(True):
        sample_routine()
        client.loop()

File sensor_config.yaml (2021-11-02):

---
'1':
  id: 1
  type: soil_humidity
  name: humidity_1
  unit: "%"
  sample_gap: 15
  adc_index: 0
  dry_value: 143
  wet_value: 80
'2':
  id: 2
  type: soil_humidity
  name: humidity_2
  unit: "%"
  sample_gap: 15
  adc_index: 1
  dry_value: 143
  wet_value: 80
'3':
  id: 3
  type: soil_humidity
  name: humidity_3
  unit: "%"
  sample_gap: 15
  adc_index: 2
  dry_value: 143
  wet_value: 80
'4':
  id: 4
  type: soil_humidity
  name: humidity_4
  unit: "%"
  sample_gap: 15
  adc_index: 3
  dry_value: 143
  wet_value: 80
'5':
  id: 5
  type: ambient_temperature
  name: ambient_temperature
  unit: "°f"
  sample_gap: 15
'6':
  id: 6
  type: ambient_humidity
  name: ambient_humidity
  unit: "%"
  sample_gap: 15
'7':
  id: 7
  type: light
  name: ambient_light
  unit: "%"
  sample_gap: 15
  adc_index: 4
  light_value: 255
  dark_value: 20

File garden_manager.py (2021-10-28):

"""Manager for the garden.

This module handles logging sensor values to the database as
well as the automation of watering events.

"""
import json
from datetime import datetime as dt

import paho.mqtt.client as mqtt
from sqlalchemy import select

from utils.common import connection_message, parse_json_payload
from utils.db_interaction import (create_plant, create_sample, create_sensor,
                                  create_watering_event, engine, initialize_db,
                                  plant_table, sensor_table, watering_table)
from utils.logging import mqtt_logger, sample_logger

# Create all of the schema objects in the database and create the engine.
initialize_db()

# IP for the MQTT broker
broker_ip = ""

# Create an MQTT client object
client = mqtt.Client("garden_manager")


def check_plants():
    """Check that every soil_humidity sensor has a plant associated with it.

    If there exists a soil_humidity sensor that does not have a plant associated,
    create a new plant with default values in the DB.
    """
    with engine.connect() as conn:
        plant_ids = conn.execute(
            select(plant_table.c.id)
        ).fetchall()
        # Convert list of tuples into list of ids.
        plant_ids = [id for id, in plant_ids]

        associated_sensor_ids = conn.execute(
            select(plant_table.c.humidity_sensor_id)
        ).fetchall()
        associated_sensor_ids = [id for id, in associated_sensor_ids]

        humidity_sensors = conn.execute(
            select(sensor_table.c.id).where(
                sensor_table.c.type == 'soil_humidity')
        ).fetchall()
        humidity_sensors = [id for id, in humidity_sensors]

        # now we have all plants and soil humidity sensors
        for humidity_sensor_id in humidity_sensors:
            # Create plants for every humidity sensor
            if humidity_sensor_id not in associated_sensor_ids:
                # Plant with default values
                create_plant({
                    # plant_ids is combined with single-element list to prevent max([])
                    "name": f"plant_{max(plant_ids + [0]) + 1}",
                    "humidity_sensor_id": humidity_sensor_id,
                    "pump_id": max(plant_ids + [0]) + 1,
                    "target": 50,
                    "watering_cooldown": 300,
                    "watering_duration": 1,
                    "humidity_tolerance": 5
                })
                # Recursive call so we don't have to keep track of generated ids
                check_plants()
                return


def check_watering(msg):
    """Check whether a plant needs to be watered by a pump

    Parameters
    ----------
    msg : dict
        Message from a soil_humidity sensor that may a prompt a watering event.
            Format:
                {
                    sensor_id: <id>,
                    timestamp: <ISO>,
                    value: <value>
                }
    """
    # Ensure that all humidity_sensors have an associated plant object.
    check_plants()

    # Select data on the plant for the given soil_humidity sensor_id
    with engine.connect() as conn:
        plant_info = conn.execute(
            select(plant_table).
            where(plant_table.c.humidity_sensor_id == msg["sensor_id"])
        ).first()

    id, name, hum_sensor_id, pump_id, target, cooldown, duration, tolerance = plant_info

    with engine.connect() as conn:
        last_watering_event = conn.execute(
            select(watering_table)
            .where(watering_table.c.plant_id == id)
            .order_by(watering_table.c.timestamp.desc())
        ).fetchone()

    # Check if plant has never been watered or if last time watered is longer than cooldown
    if (not last_watering_event or (msg["timestamp"] - last_watering_event["timestamp"]).total_seconds() > cooldown):
        # Check if the soil humidity is less than target - tolerance
        if (msg["value"] < target - tolerance):
            payload = {
                "duration": duration
            }
            mqtt_logger.info(
                f"Published to pumps/control/{pump_id}: {json.dumps(payload, indent=4)}")
            client.publish(
                f"pumps/control/{pump_id}", payload=json.dumps(payload), qos=2)


def handle_pumps_control(client, userdata, msg):
    """Log a watering event in the database."""
    payload = parse_json_payload(msg)
    mqtt_logger.info(
        f"Received pump event for pump_id {msg.topic.split('/')[-1]}: {json.dumps(payload, indent=4)}")

    with engine.connect() as conn:
        result = conn.execute(
            select(plant_table.c.id).where(
                plant_table.c.id == int(msg.topic.split("/")[-1])
            )
        )
        plant_id = result.fetchone()[0]
    payload.update(
        {
            "timestamp": dt.now(),
            "plant_id": plant_id
        }
    )
    create_watering_event(payload)


def handle_plants_config(client, userdata, msg):
    """Update the DB to save plant configs."""
    payload = parse_json_payload(msg)
    mqtt_logger.info(f"Received plant config: {json.dumps(payload, indent=4)}")
    create_plant(payload)


def handle_sensors_config(client, userdata, msg):
    """Update the DB with a new sensor config, then broadcast a new 'sensors/info'."""
    payload = parse_json_payload(msg)
    mqtt_logger.info(
        f"Received sensor config: {json.dumps(payload, indent=4)}")
    payload.update(
        {
            "id": int(payload["id"]),
            "sample_gap": int(payload["sample_gap"])
        }
    )
    create_sensor(payload)
    publish_sensor_info()


def handle_sensors_data(client, userdata, msg):
    """Log received data into the DB as a new data sample."""
    payload = parse_json_payload(msg)
    sample_logger.info(
        f"Received {payload['value']} from sensor_id {msg.topic.split('/')[-1]}")

    payload.update(
        {
            "sensor_id": msg.topic.split("/")[-1],
            "timestamp": dt.fromisoformat(payload["timestamp"])
        }
    )

    create_sample(payload)

    with engine.connect() as conn:
        result = conn.execute(
            select(sensor_table.c.type)
            .where(sensor_table.c.id == payload["sensor_id"])
        ).fetchone()

    if result[0] == "soil_humidity":
        # Check if the plant needs to be watered
        check_watering(payload)


def publish_status(client, userdata, flags, rc):
    """Publish the status of garden_manager."""
    mqtt_logger.info(connection_message(broker_ip, rc))
    client.publish("status/garden_manager",
                   payload="online", qos=2, retain=True)
    mqtt_logger.info("Published status")
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

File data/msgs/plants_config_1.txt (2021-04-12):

{
    "id": 1,
    "name": "Rosemary",
    "humidity_sensor_id": 1,
    "pump_id": 1,
    "target": 56,
    "watering_cooldown": 60,
    "watering_duration": 3,
    "humidity_tolerance": 5
}

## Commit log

2021-03-30 added fritzing schematic
2021-04-07 Basics of SQLAlchemy
    [example_data.csv]
2021-04-08 Added sensor MQTT sending to configuration.py
2021-04-08 deleted pycache
    [iot_herb_garden_schematic.fzz]
2021-04-11 Added sampling logic to garden_monitor, missing MQTT
    [garden_monitor.py]
2021-04-12 Completed garden_manager.py
    [plants_config_1.txt, sensors_config_1.txt]
2021-04-13 Added utility functions for sensors to make it easier to use them. Added temp.py to show example usage.
2021-04-14 Reworked garden_monitor. Added logging.
    [sensors_config_1.txt]
2021-04-19 *WIP* Updating history to display sensor data.
    [example_data.csv]
2021-04-20 Added plant checking functionality
    [sensors_config_1.txt]
2021-04-20 Mostly finished configurations, needs format sensors rate
2021-04-22 fixed loading sample rate to display using samples per rate format
2021-04-24 Fixed double-sampling issue in garden_monitor and occasional crash because of ADC.
    [adc_library.py, garden_monitor.py, sensors.py]
